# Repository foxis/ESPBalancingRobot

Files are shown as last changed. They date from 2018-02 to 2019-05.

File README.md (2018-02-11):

# ESPBalancingRobot
ESP8266 ESP-1 WiFi Balancing robot

Originally the robot was built using Arduino pro mini and all it could do was balance. I was thinking to add BT module to control it until I discovered that I have ESP8266 lying around. Also I decided to use a better IMU algorithm instead of DPU of the MPU6050.
Thus the ESPBalancingRobot was born.

# Configuration before Building
Before building and uploading please create `wificonfig.h` file with the following contents:
```
#define WIFI_SSID        "ssid"
#define WIFI_PASSWORD    "password"
#define ARDUINO_HOSTNAME "hostname"
```

If you fork the repo, you can still have this file as it is in `.gitignore` and won't be added during commit.

# Building and flashing

PlatformIO was used to develop the code, therefore the structure of the project conforms to what PlatformIO expects.
Flash the ESP module first before soldering anything. Also upload SPIFFS.
After that it is possible to use OTA, just don't forget to configure ESP to connect to your local network.
You can start assembling the robot.

# Construction

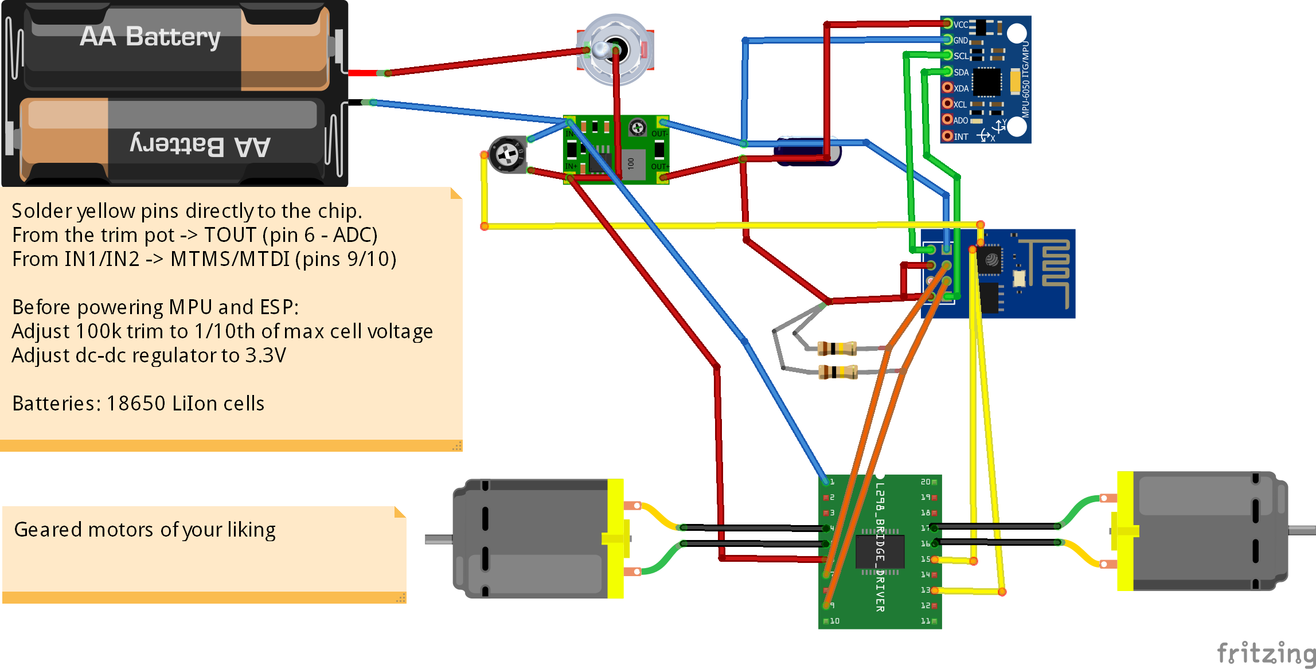
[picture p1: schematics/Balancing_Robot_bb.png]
Schematics of the robot


## Wheel base

Wheel base consists of two geared motors, some scrap wheels and a 3D printed motor holder which is basically a tube with slots
to hold wooden sheet. Later I added pads so that the robot wouldn't suffer much after falling over.

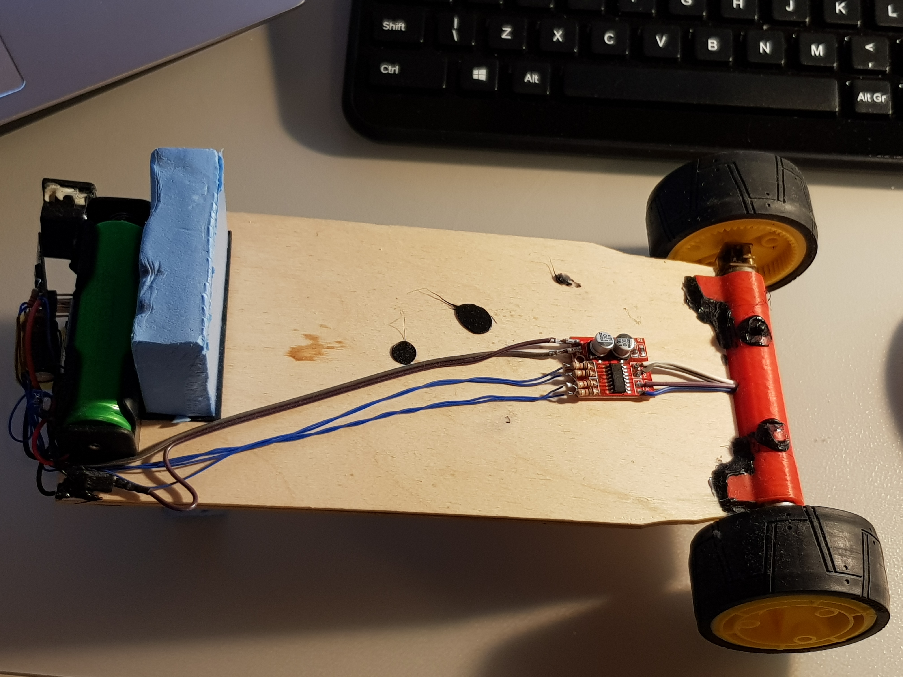
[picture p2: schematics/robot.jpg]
Overview of the robot


## Motor controller

I used a 1A motor controller based on L293, however chinese manufacturers seemed to be too secretive about the chip used... Even though they advertise it as L293 motor controller board on ebay :)

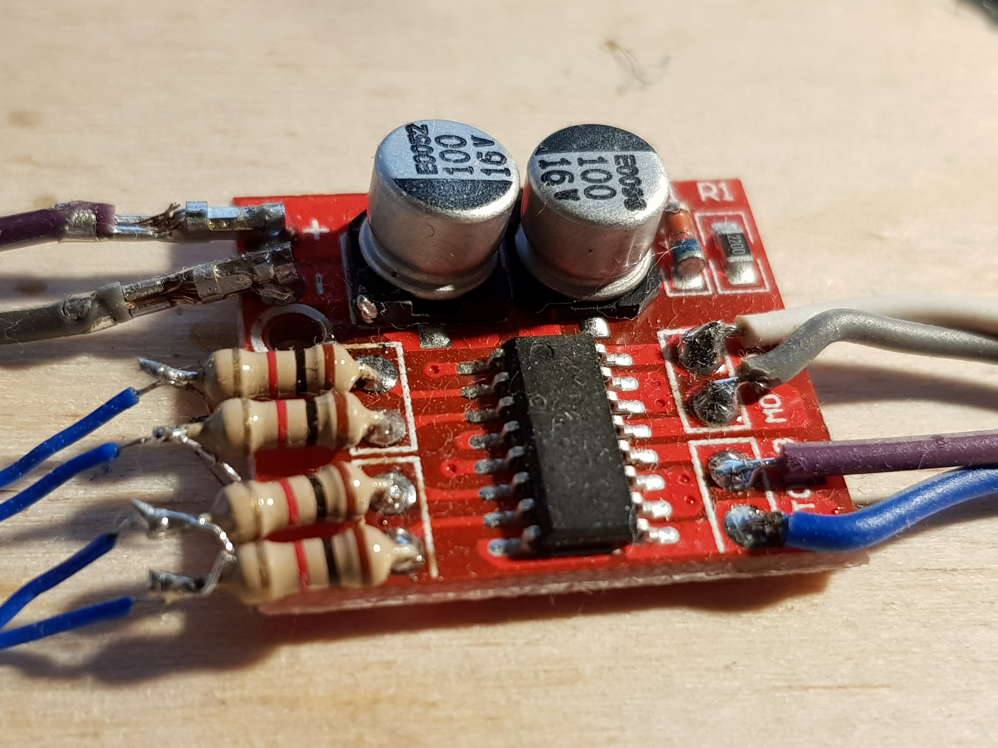
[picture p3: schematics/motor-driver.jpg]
Motor controller


## Electronics
The robot is powered by two LiIon batteries salvages from old laptop battery. There is a dc-dc buck converter that supplies 3.3V for electronics, some random power switch, ESP-1 module and an MPU6050 board. Also some pullups, capacitors and a trim potentiometer for battery monitoring (turned down to 1:10 ratio).

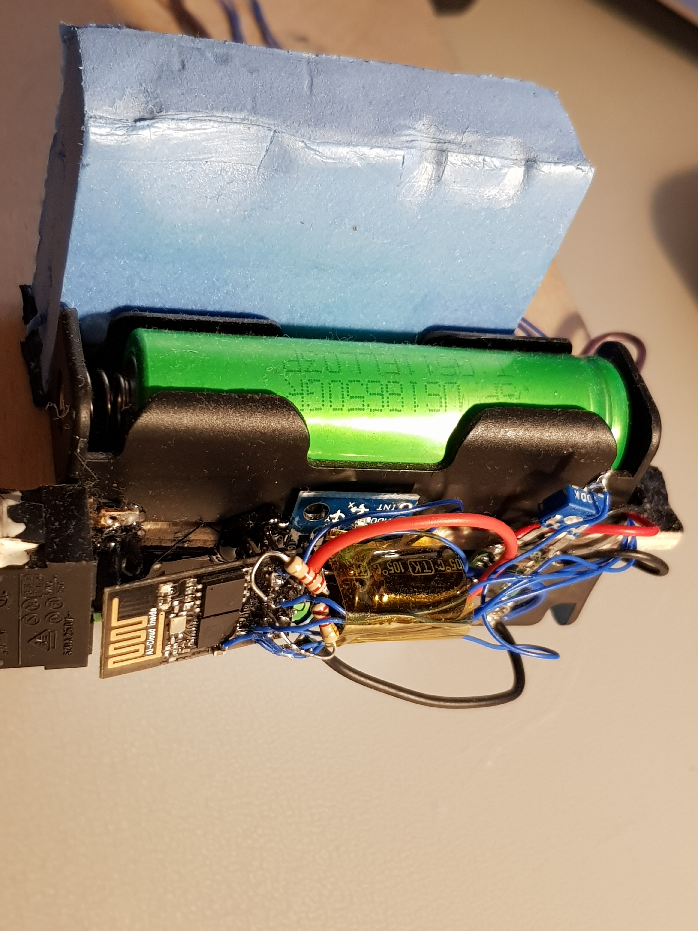
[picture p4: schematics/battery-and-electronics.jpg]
Battery, some bumpers and electronics


IMU was used a simple MPU6050 and can be seen under the ESP module. It is glued by hot glue to the battery holder. Alignment is not perfect, but staged PID adjusts for that.

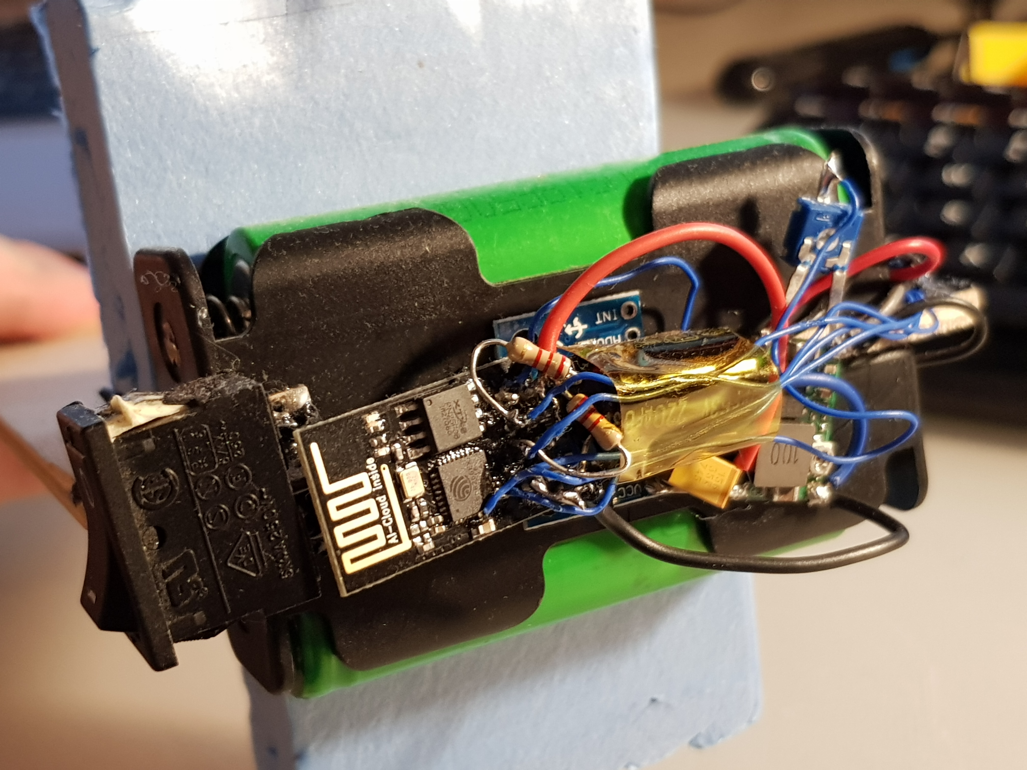
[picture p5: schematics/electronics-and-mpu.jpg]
Robot brains


## The ESP-1 module

For robot control we need six pins(not counting ADC pin for battery monitoring): 2x for I2C, 4x for PWM control.
As ESP-1 module clearly doesn't have enough pins we need to add those. With a steady hand, small soldering iron, some flux and good eyes it is possible to solder those additional ports directly to the ESP chip pins.

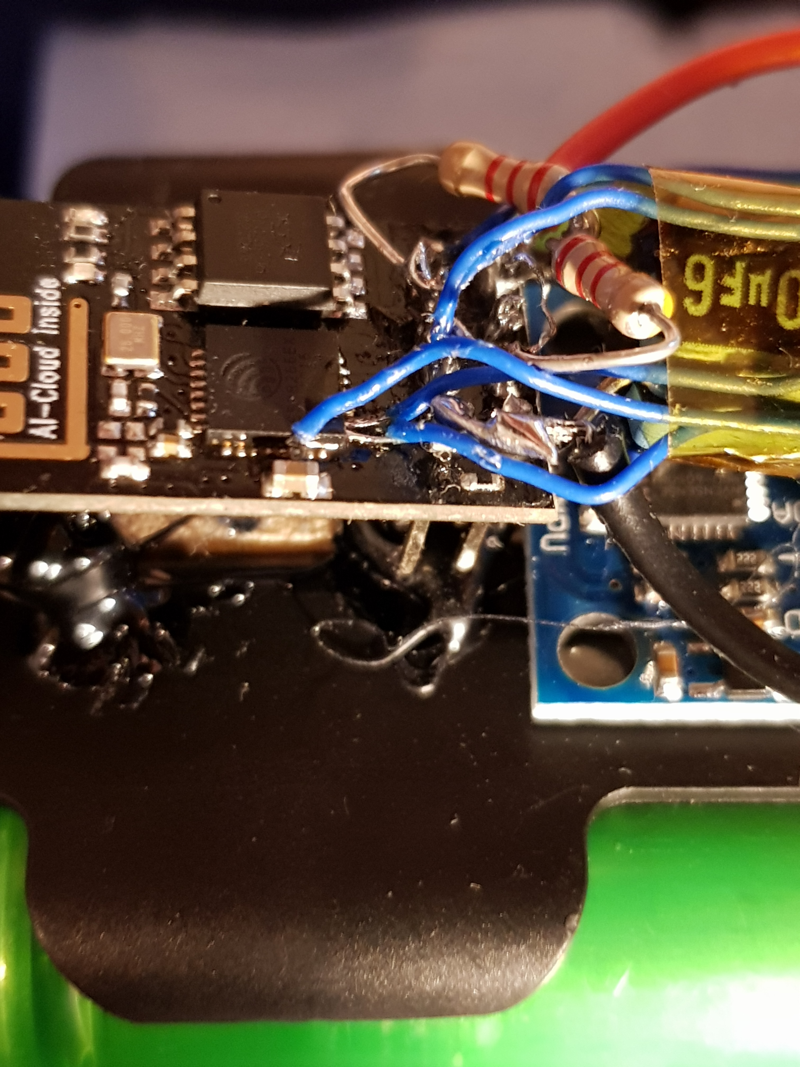
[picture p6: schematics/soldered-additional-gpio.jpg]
Additional GPIO soldered directly to the chip pins


I used RX/TX pins for I2C as the chip emits some noise on those pins while booting and MPU doesn't seem to be upset about that. Although the motors might be.

Also I had to add pullUP resistors to GPIO0 and GPIO2 and a beafy capacitor on the 3.3V rail.

One thing to mention about the motors. For some reason one of my motor drivers and ESP modules during the early stages of the build just died on me. I figured that it had something to do with cheap motor driver burnup. So this time I added 1k resistors in series just to be safe.

# Theory of operation

Mostly inspired by `https://www.reddit.com/r/esp8266/comments/5pqri1/espway_a_selfbalancing_robot_powered_by_esp8266/`.

# PID tuning

It is possible to tune PID controllers by building the firmware with

```
#define USE_LOGGING 1
```

somewhere in the beginning of the code.
The UI changes somewhat and allows to see the realtime graphs of speed/angle values and also provides some sliders to set pid values.
There are some issues, though with the ESPUI, as if I add all the controllers (for both PIDs), the ESP crashes. Also adding all the desired controls consumes to much flash size so the OTA doesn't allow to flash due to size limitations.

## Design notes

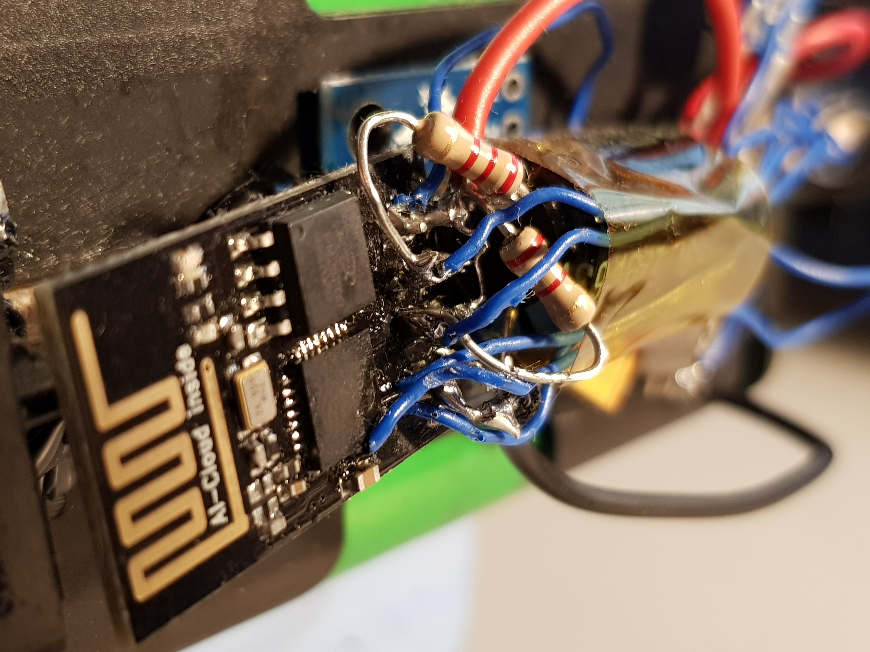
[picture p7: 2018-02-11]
schematics/esp8266.jpg

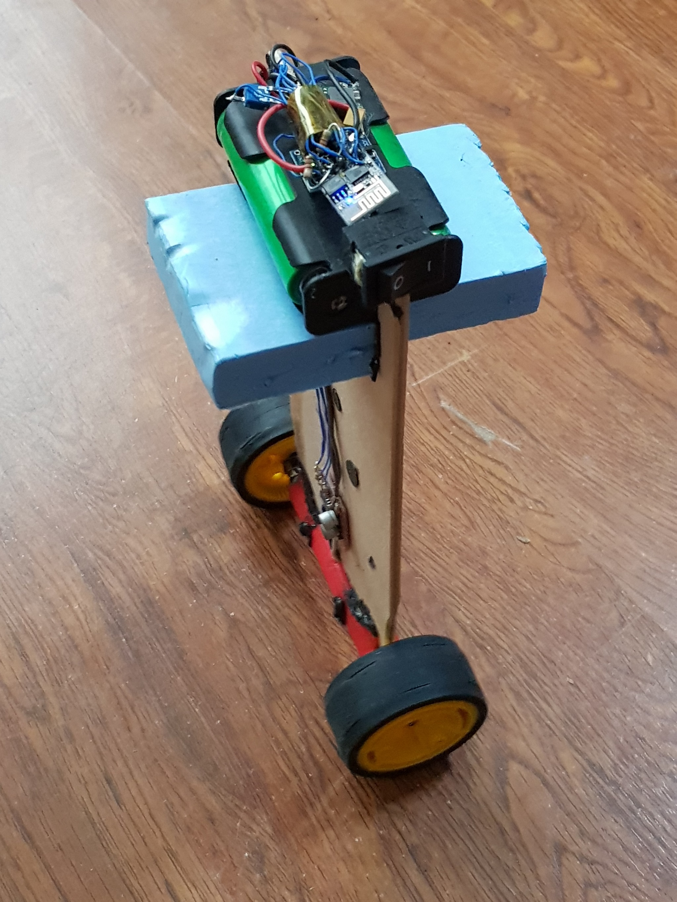
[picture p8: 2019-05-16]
schematics/espbalancer.jpg

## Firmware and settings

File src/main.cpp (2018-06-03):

/*  ESPBalancingRobot
 *
 *  Copyright (C) 2018  foxis (Andrius Mikonis <andrius.mikonis@gmail.com>)
 *
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
 */

#include <EasyOTA.h>
#include <ESPAsyncWebServer.h>
#include <SPIFFSEditor.h>
#include "DiffDriveBalancerNoEnc.h"

#ifndef USE_LOGGING
#include <ESPUI.h>
#endif

#include "wificonfig.h"

#define LABEL_HEARTBEAT "Heart Beat:"
#define LABEL_VOLTAGE "Analog voltage:"
#define LABEL_INCLINATION "Inclination:"
#define LABEL_SPEED "Speed:"
#define LABEL_HEADING "Heading:"
#define MOTOR_A0  14
#define MOTOR_B0  12
#define MOTOR_A1  0
#define MOTOR_B1  2
#define IMU_ADDR 0x68
#define IMU_SDA   3
#define IMU_SCL   1

EasyOTA OTA(ARDUINO_HOSTNAME);
Locomotion::DiffDriveBalancerNoEncoders robot(500, IMU_SDA, IMU_SCL, IMU_ADDR, MOTOR_A0, MOTOR_B0, MOTOR_A1, MOTOR_B1, 24.0);
#ifdef USE_LOGGING
AsyncWebServer logger_server(80);
AsyncWebSocket logger("/log");
#endif

void heartBeat(unsigned long now) {
  static long prevMillis = 0;
  static bool dotState = 0;

  if ( now - prevMillis > 500000 ) {
    prevMillis = now;
		#ifndef USE_LOGGING
    //dotState = !dotState;
    //ESPUI.print(LABEL_HEARTBEAT, dotState ? "Ping" : "Pong");

    ESPUI.print(LABEL_INCLINATION, robot.getInclination());
    ESPUI.print(LABEL_SPEED, robot.getSpeed());
    ESPUI.print(LABEL_HEADING, robot.getHeading());
    ESPUI.print(LABEL_VOLTAGE, String(10.0 * (analogRead(A0) / 1024.0)));
		#endif
  }
}

#ifndef USE_LOGGING

void speedSlider(Control sender, int type) {
  robot.setSpeed(0.5f * (sender.value.toInt() / 100.0f - .5f));
}
void headingSlider(Control sender, int type) {
  robot.setHeading(2.0f * (sender.value.toInt() / 100.0f - .5f));
}

double ip=0, ii=0, id=0;
double sp=0, si=0, sd=0;

void ipSlider(Control sender, int type) { ip = 25.0 * sender.value.toInt() / 100.0;  robot.setInclinationPID(ip, ii, id); }
void iiSlider(Control sender, int type) { ii = 25.0 * sender.value.toInt() / 100.0;  robot.setInclinationPID(ip, ii, id); }
void idSlider(Control sender, int type) { id = sender.value.toInt() / 100.0;  robot.setInclinationPID(ip, ii, id); }

void spSlider(Control sender, int type) { sp = 10 * sender.value.toInt() / 100.0;  robot.setSpeedPID(sp, si, sd); }
void siSlider(Control sender, int type) { si = sender.value.toInt() / 100.0;  robot.setSpeedPID(sp, si, sd); }
void sdSlider(Control sender, int type) { sd = sender.value.toInt() / 100.0;  robot.setSpeedPID(sp, si, sd); }

void inclinationSlider(Control sender, int type) { robot.setInclination((sender.value.toInt() / 100.0f - .5f) / 4.0); }

#endif

void setup() {
  robot.begin();

  OTA.addAP(WIFI_SSID, WIFI_PASSWORD);

#ifndef USE_LOGGING
  //ESPUI.label(LABEL_HEARTBEAT, COLOR_TURQUOISE, "Ping");
  ESPUI.label(LABEL_VOLTAGE, COLOR_TURQUOISE, "0.0");
  ESPUI.label(LABEL_INCLINATION, COLOR_TURQUOISE, "-");
  ESPUI.label(LABEL_SPEED, COLOR_TURQUOISE, "-");
  ESPUI.label(LABEL_HEADING, COLOR_TURQUOISE, "-");
	//ESPUI.slider("Inclination", &inclinationSlider, COLOR_NONE, "31");
  ESPUI.slider("Speed", &speedSlider, COLOR_NONE, "50");
  ESPUI.slider("Heading", &headingSlider, COLOR_NONE, "50");

	//ESPUI.slider("I P", &ipSlider, COLOR_NONE, "35");
	//ESPUI.slider("I I", &iiSlider, COLOR_NONE, "0");
	//ESPUI.slider("I D", &idSlider, COLOR_NONE, "9");

	//ESPUI.slider("S P", &spSlider, COLOR_NONE, "0");
	// ESPUI.slider("S I", &siSlider, COLOR_NONE, "0");
	//ESPUI.slider("S D", &sdSlider, COLOR_NONE, "0");

  ESPUI.begin("BRC", false);
#endif

#ifdef USE_LOGGING
	SPIFFS.begin();
	logger.onEvent([](AsyncWebSocket * server, AsyncWebSocketClient * client, AwsEventType type, void * arg, uint8_t *data, size_t len){
		if (type == WS_EVT_DATA && strcmp((char *)data, "get-data") == 0)
		{
			log_t log[LOG_SIZE];
			char buf[255];
			size_t size = robot.dump_log((log_t *)log, 1);

			for (size_t i=0; i < size; i++)
			{
				sprintf(buf, "{\"now\":%u,\"ci\":%.5f, \"ti\":%.5f, \"cs\":%.5f, \"fc\":%.5f, \"ts\":%.5f}",
				  log[i].now,
					log[i].currentInclination, log[i].targetInclination,
					log[i].currentSpeed, log[i].fwdControl, log[i].targetSpeed
				);
				client->text(buf);
			}
		}
	});
	logger_server.addHandler(&logger);
	logger_server.serveStatic("/", SPIFFS, "/").setDefaultFile("log.html");
	// Heap for general Servertest
	logger_server.on("/heap", HTTP_GET, [](AsyncWebServerRequest *request) {
		request->send(200, "text/plain", String(ESP.getFreeHeap()));
	});

	logger_server.onNotFound(
			[](AsyncWebServerRequest *request) { request->send(404); });
	logger_server.begin();
#endif
}

void loop() {
  unsigned long now = micros();

  OTA.loop(now);

  heartBeat(now);
  robot.loop(now);
}

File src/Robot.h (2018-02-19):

/*  ESPBalancingRobot
 *
 *  Copyright (C) 2018  foxis (Andrius Mikonis <andrius.mikonis@gmail.com>)
 *
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
 */

#include <Wire.h>
#include <MadgwickAHRS.h>
#include <PID_v1.h>
#define SENSORS_MPU6050_ATTACHED
#include <Sensors.h>
#include <math.h>
#include "DiffDrive.h"

#define MPU_addr 0x68
#define MOTOR_A0  14
#define MOTOR_B0  12
#define MOTOR_A1  0
#define MOTOR_B1  2
#define IMU_SDA   3
#define IMU_SCL   1

//#define USE_LOGGING 1

#define STABILIZING_TIMEOUT 2000000
#define INCLINATION_THRESHOLD .6

#ifdef USE_LOGGING
#define LOG_SIZE 4
typedef struct log_struct
{
	unsigned long now;
	float targetInclination;
	float currentInclination;
	float fwdControl;
	float targetSpeed;
	float currentSpeed;
} log_t;
#endif

class Robot
{
  Madgwick filter;
  DiffDrive ddrive;
  PID pidInclination;
  PID pidHeading;
  PID pidSpeed;

  long prevTimeStamp;
  long duration;
  long fps;
	unsigned long stabilizingStart = 0;

  // PID input/output/target
  double currentInclination = 0, fwdControl, targetInclination = -.0475;
  double currentHeading = 0, headingControl, targetHeading = 0;
  double currentSpeed = 0, targetSpeed = 0;
	bool stabilizing = true;

#ifdef USE_LOGGING
	volatile bool dumping = false;
	volatile bool logging = false;
	size_t log_tail = 0, log_head = 0, log_size = 0;
	log_t log[LOG_SIZE];
#endif

public:
  Robot(long fps, double wheelBase)
	//:pidInclination(&currentInclination, &fwdControl, &targetInclination, 8.0, 0.0, 0.09, DIRECT),
    :pidInclination(&currentInclination, &fwdControl, &targetInclination, 5.0, 19.0, 0.09, DIRECT),
    pidHeading(&currentHeading, &headingControl, &targetHeading, 0.1, 0.0, 0.001, DIRECT),
    pidSpeed(&currentSpeed, &targetInclination, &targetSpeed, .4, .6, 0.01, REVERSE),
    ddrive(MOTOR_A0, MOTOR_B0, MOTOR_A1, MOTOR_B1, wheelBase)
  {
    this->fps = fps;
    duration = 1000000L / fps;
    pidSpeed.SetOutputLimits(-.5, .05);
    pidHeading.SetOutputLimits(-1, 1);
    pidInclination.SetOutputLimits(-1, 1);
    pidInclination.SetSampleTime(duration);
    pidSpeed.SetSampleTime(duration);
    pidHeading.SetSampleTime(duration);
    pidInclination.SetMode(AUTOMATIC);
    pidSpeed.SetMode(AUTOMATIC);
    pidHeading.SetMode(AUTOMATIC);
  }

  void begin()
  {
    Wire.begin(IMU_SDA, IMU_SCL);
    Wire.setClock(400000);
    filter.begin(fps);

    Sensors::initialize();

    ddrive.init();
    prevTimeStamp = micros();
  }

  void loop(unsigned long now)
  {
    if ( now - prevTimeStamp > duration ) {
			#ifdef USE_LOGGING
						logging = true;
						if (log_size < LOG_SIZE && !dumping)
						{
							log[log_head].now = now;
							log[log_head].currentInclination = (float)currentInclination;
							log[log_head].targetInclination = (float)targetInclination;
							log[log_head].fwdControl = (float)fwdControl;
							log[log_head].currentSpeed = (float)currentSpeed;
							log[log_head].targetSpeed = (float)targetSpeed;
							log_head = (log_head + 1) % LOG_SIZE;
							log_size ++;
						}
						logging = false;
			#endif

			DetermineOrientation();

			if (stabilizing || fabs(currentInclination) > INCLINATION_THRESHOLD) {
				if (now - stabilizingStart > STABILIZING_TIMEOUT && stabilizingStart != 0 && fabs(currentInclination) < INCLINATION_THRESHOLD)
					stabilizing = false;
				else {
					ddrive.setDiffSpeed(0, 0);
					fwdControl = 0;
					targetInclination = -.0475;
					pidInclination.Reset();
					pidHeading.Reset();
					pidSpeed.Reset();
					if (fabs(currentInclination) > INCLINATION_THRESHOLD)
					{
						stabilizingStart = now;
						stabilizing = true;
					}
				}
			}
			DetermineSpeed();

      pidSpeed.Compute(now);
      pidHeading.Compute(now);
      pidInclination.Compute(now);
			if (!stabilizing)
      	ApplyControls();
			prevTimeStamp = now;
    }
  }

  //
  // Control methods
  //
  void setSpeed(double speed)
  {
    targetSpeed = speed;
  }
	void setHeading(double heading)
  {
    targetHeading = heading;
  }
	void setInclination(double incl)
  {
    targetInclination = incl;
  }

  //
  // control parameters
  //
  void setInclinationPID(double P, double I, double D)
  {
    pidInclination.SetTunings(P, I, D);
  }
  void setSpeedPID(double P, double I, double D)
  {
    pidSpeed.SetTunings(P, I, D);
  }
  void setHeadingPID(double P, double I, double D)
  {
    pidHeading.SetTunings(P, I, D);
  }

  //
  // Diagnostics methods
  //
  double getRollRadians()
  {
    return filter.getRollRadians();
  }
  double getYawRadians()
  {
    return filter.getYawRadians();
  }
  double getPitchRadians()
  {
    return filter.getPitchRadians();
  }

  String formatString(float current, float target)
  {
    char tmp[64];
    sprintf(tmp, "%.03f - %.03f", current, target);
    return String((char *)tmp);
  }
  String getInclination()
  {
    return formatString(currentInclination, targetInclination);
  }

  String getHeading()
  {
    return formatString(currentHeading, targetHeading);
  }

  String getSpeed()
  {
    return formatString(currentSpeed, targetSpeed);
  }

#ifdef USE_LOGGING
	size_t dump_log(log_t* data, size_t size)
	{
		if (logging) return 0;

		dumping = true;
		size_t i = 0;
		size_t real_size = min(log_size, size);

		for (i = 0; i < real_size; i++)
		{
			memcpy(data + i, log + (log_tail + i) % LOG_SIZE, sizeof(log_t));
		}
		log_tail = (log_tail + real_size) % LOG_SIZE;
		log_size -= real_size;

		dumping = false;
		return real_size;
	}
#endif

private:
  double softcap(double x)
  {
    //double ex = exp(5 * x);
    //return 2.0 * ex / (1.0 + ex) - 1;
		if (x > 1.0)
			return 1.0;
		else if (x < -1.0)
			return -1.0;
		else
			return x;
  }

  void ApplyControls()
  {
		double motor = softcap(fwdControl);
		double eps = .01;
		if (motor > eps)
			motor += .17;
		else if (motor < -eps)
			motor -= .17;
    ddrive.setDiffSpeed(motor, softcap(headingControl));
  }

  void DetermineSpeed()
  {
		double alpha = .01;
		double drive_speed = fwdControl; //ddrive.getSpeed();
    currentSpeed = currentSpeed * (1.0 - alpha) + drive_speed * alpha;
  }

  int DetermineOrientation()
  {
    Accelerometer *acc = Sensors::getAccelerometer();
    Gyroscope *gyro = Sensors::getGyroscope();

    Vector3 a, r;

    if (acc)
      a = acc->getAcceleration();
    if (gyro)
      r = gyro->getRotation();

    filter.updateIMU(r.x, r.y, r.z, a.x, a.y, a.z);

		//double alpha = .5;
		//double roll = getRollRadians();
    //currentInclination = (1 - alpha) * currentInclination + roll * alpha;
    currentInclination = getRollRadians();

    return 0;
  }
};

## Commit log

2018-02-11 Initial code commit
    [Balancing Robot.fzz]
2019-05-16 ADD: Missing schematic.

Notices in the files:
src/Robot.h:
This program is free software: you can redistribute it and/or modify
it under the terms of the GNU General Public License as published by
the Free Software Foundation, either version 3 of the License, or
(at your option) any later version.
